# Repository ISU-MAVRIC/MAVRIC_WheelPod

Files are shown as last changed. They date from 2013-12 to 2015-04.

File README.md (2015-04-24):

MAVRIC_WheelPod
===============

Each MAVRIC Wheel Pod contains a motor controller driving the wheel along with a stepper to rotate the entire pod, steering the rover. This board controls these components in a compact, modular form factor. One will be located at each of the six wheel pods.

**Features:**
- STM32F4 Microcontroller
- PWM output to motor driver controlling wheel speed
- Current measurement on motor driver to measure wheel traction
- Stepper motor output to rotate the wheel pod, steering the rover
- Encoder analog in for steering position feedback, fed into a control loop
- RJ45 Jack for rx/tx control/status data as well as powering the wheel pod's 3V3 and 5V rails

##PCB Progress:
### Wheel Pod Board v1.0 ordered!
https://github.com/ISU-MAVRIC/MAVRIC_WheelPod/releases/tag/v1.0

Current Price: $12.60 for 3 boards, $4.20 each

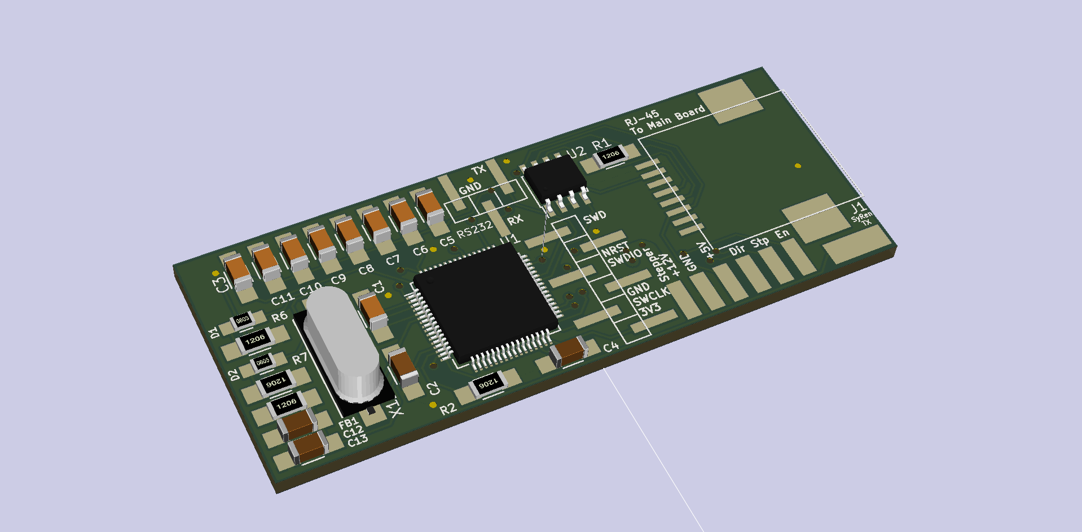
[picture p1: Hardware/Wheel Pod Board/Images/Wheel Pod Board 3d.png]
Board 3D


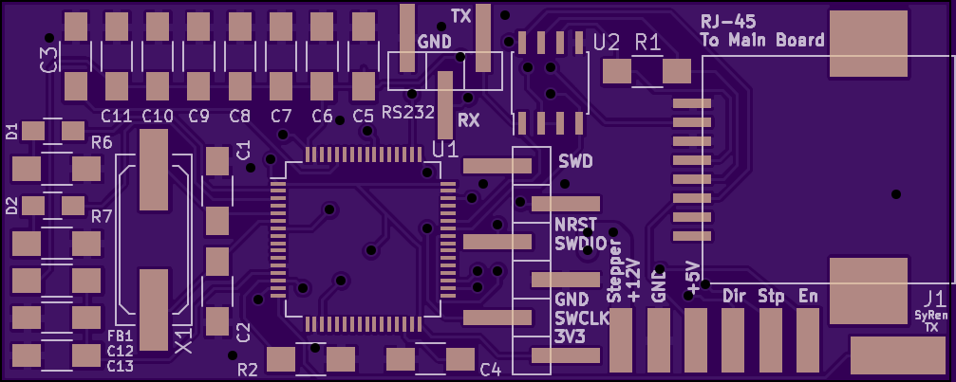
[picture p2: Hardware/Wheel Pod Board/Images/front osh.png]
'Wheel Pod Board Front
<br>
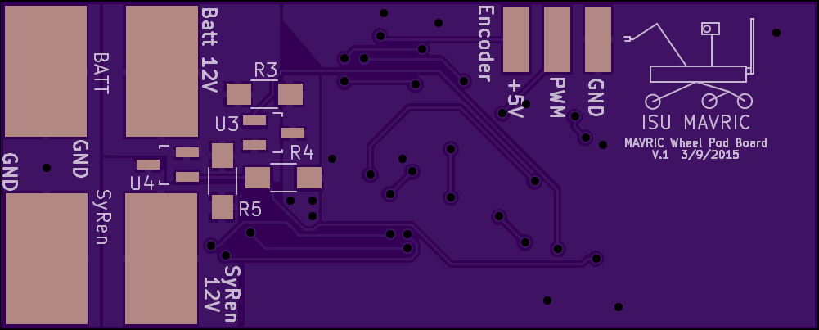
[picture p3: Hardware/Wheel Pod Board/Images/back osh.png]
Wheel Pod Board Back


### Grid Settings
- .5mm layout
- .5mm traces when possible, down to .25mm for detailed routing

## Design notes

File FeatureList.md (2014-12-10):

# Wheel Pod Feature List
## Hardware
- Full Duplex RS-485/RS-422 Converter 3.3V Supply
- _Intersil ISL83490IBZ_
- Half Duplex RS-485/RS-422 Transceiver 5V supply
- _STMicroelectronics ST485CDR_
- Hall Effect Current Transducer
- _Allegro MicroSystems ACS711ELCTR-25AB-T_
- Inductance to Digital Converter
- _Texas Instruments LDC1000_
- 3.3v Regulator
- _STMicroelectronics L78L33ACUTR_
- 5v Regulator (Required for analog voltage on LDC)
- _STMicroelectronics L78M05CDT-TR_
- Microcontroller
- _STMicroelectronics STM32F030K6T6_

## Features
- Cat5 jack for input from Chipkit (RS-485, 3.3V, GND)
- Stepper Motor current sense
- Wheel Motor current sense
- Serial connection to SyRen
- Connection to stepper controller (Enable, Direction, Step, 3.3V)
- Specification suggests 5V, any voltage is fine as long as current is between 5 - 20mA
- Inductance sensor for wheel rotation position

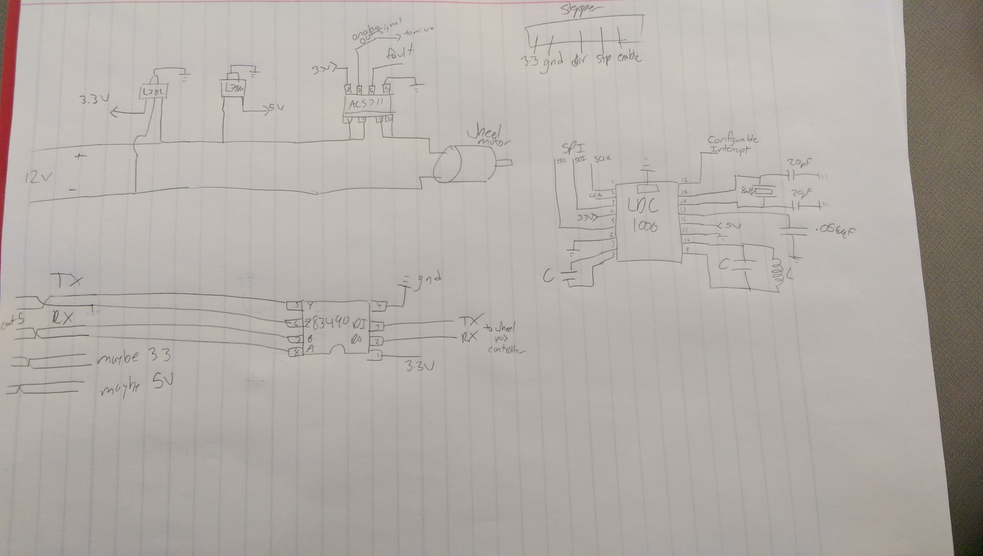
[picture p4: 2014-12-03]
Hardware/Diagrams/12-03-14 Schematic on Paper.jpg

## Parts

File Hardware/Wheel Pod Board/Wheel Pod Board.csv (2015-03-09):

Digi-Key Part Number | Customer Reference | Quantity 1
587-2254-1-ND | C4 C8 | 2
1276-2854-1-ND | C3 C5 C6 C7 C9 C10 C11 C12 | 8
240-2412-1-ND | FB1 | 1
399-8148-1-ND | C13 | 1
P100ECT-ND | R1 R6 R7 | 3
887-2439-1-ND | X1 | 1
1276-2809-1-ND | C2 C1 | 2
989-1025-1-ND | R3 | 1
P8.06KFCT-ND | R2 R4 | 2
696-1373-1-ND | R5 | 1
475-1415-1-ND | D1 | 1
475-1410-1-ND | D2 | 1

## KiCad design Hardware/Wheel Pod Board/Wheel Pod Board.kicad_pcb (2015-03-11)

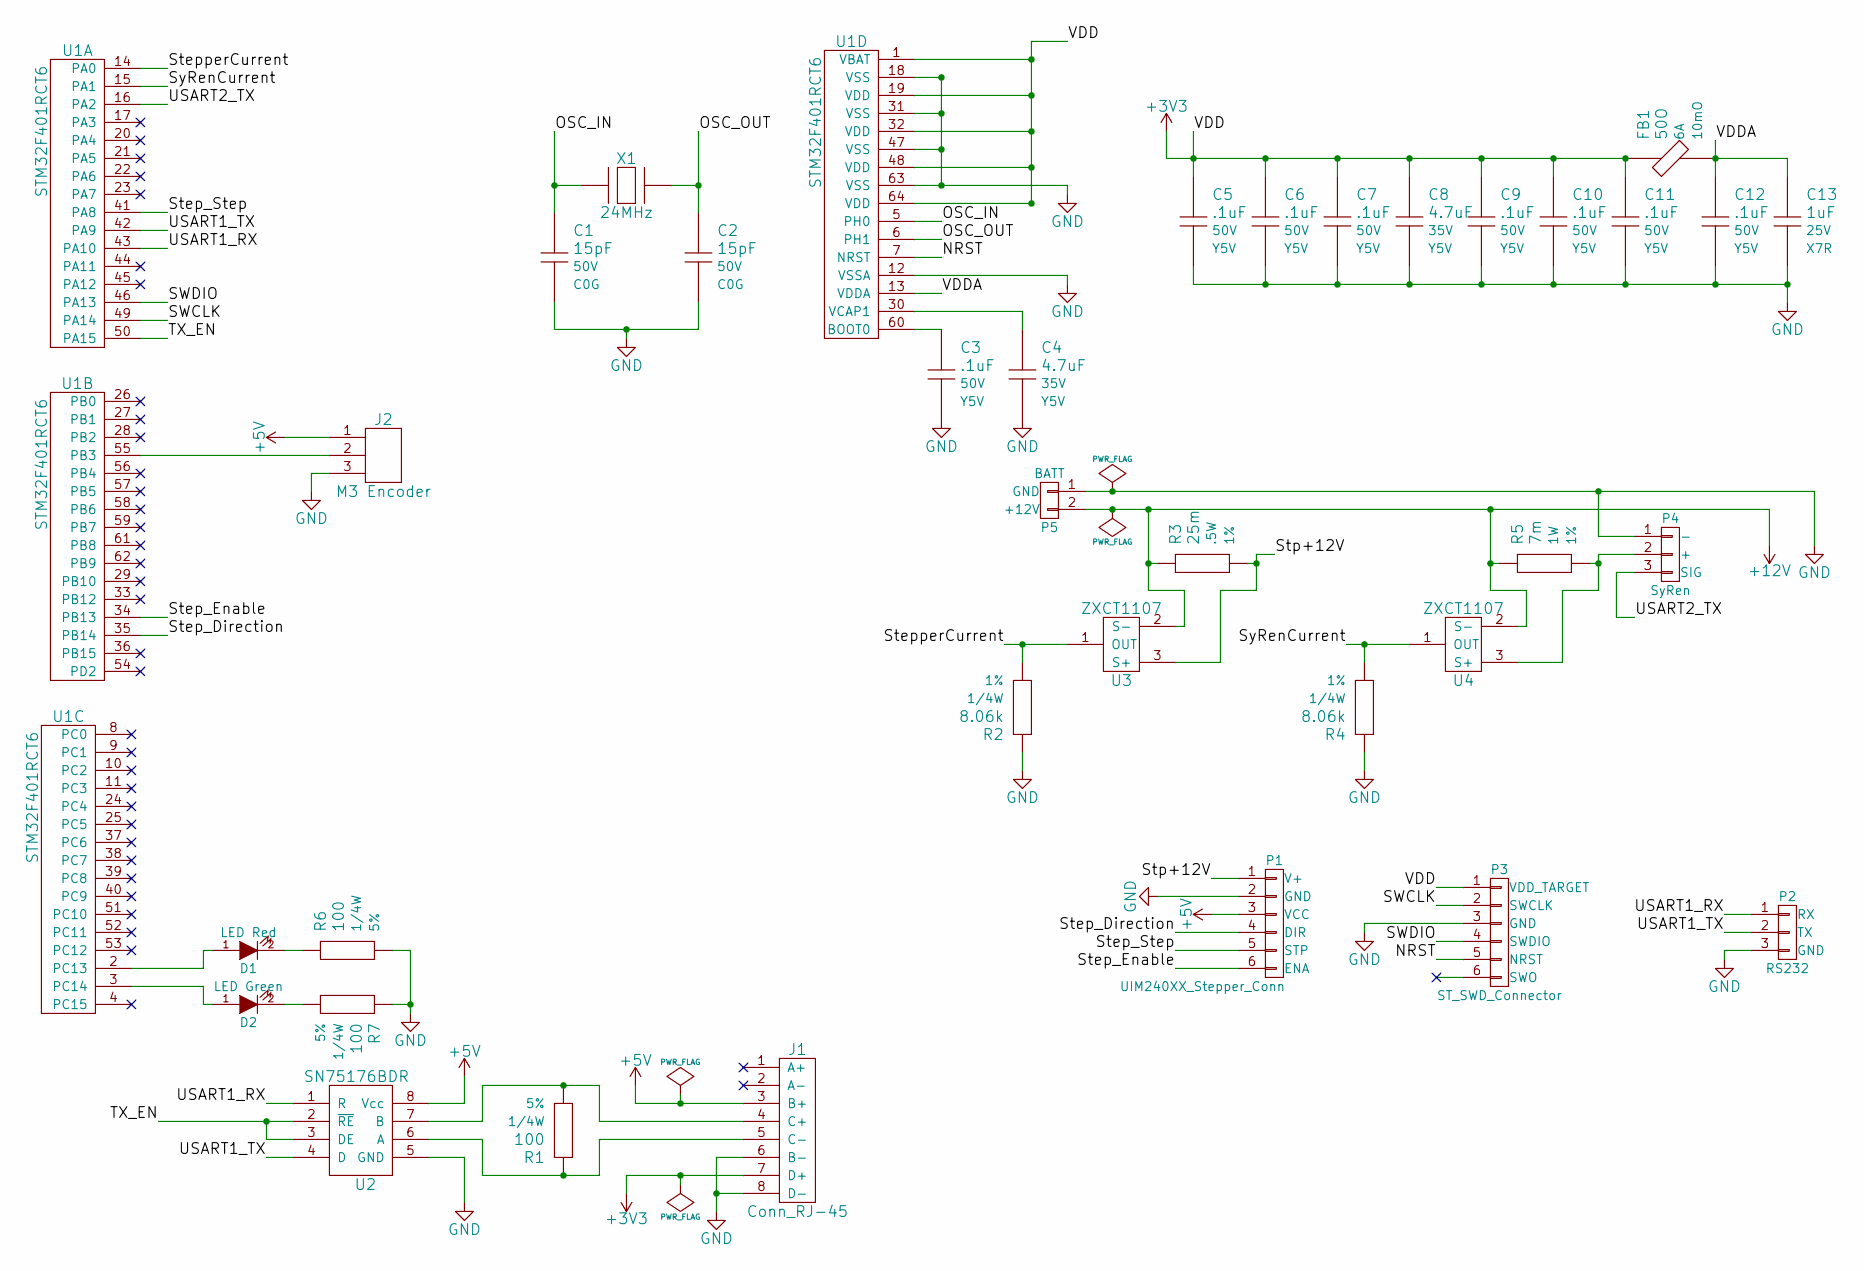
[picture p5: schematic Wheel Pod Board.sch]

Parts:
C1, C2: 15pF; C_1206_HandSoldering; Voltage 50V; Manufacturer Part # CL31C150JBCNNNC
C3, C5, C6, C7, C9, C10, C11, C12: .1uF; C_1206_HandSoldering; Voltage 50V; Manufacturer Part # CL31F104MBCNNNC
C4, C8: 4.7uF; C_1206_HandSoldering; Voltage 35V; Manufacturer Part # GMK316F475ZG-T
C13: 1uF; C_1206_HandSoldering; Voltage 25V; Manufacturer Part # C1206C105M3RACTU
D1: LED Red; R_0805_HandSoldering
D2: LED Green; R_0805_HandSoldering
FB1: 50O; R_1206_HandSoldering; Manufacturer Part # HI1206T500R-10
J1: Conn_RJ-45; Molex_RJ45_0437438101
J2: M3 Encoder; SolderWirePad_3x_0-8mmDrill
P1: UIM240XX_Stepper_Conn; 1x6_Breakaway_Header
P2: RS232; 1x3_Breakaway_Header
P3: ST_SWD_Connector; 1x6_Breakaway_Header
P4: SyRen; SolderWirePad_3x_0-8mmDrill
P5: BATT; SolderWirePad_2x_0-8mmDrill
R1, R6, R7: 100; R_1206_HandSoldering; Tolerance 5%; Manufacturer Part # ERJ-8GEYJ101V
R2, R4: 8.06k; R_1206_HandSoldering; Tolerance 1%; Manufacturer Part # ERJ-8ENF8061V
R3: 25m; R_1206_HandSoldering; Tolerance 1%; Manufacturer Part # LRC-LRF1206LF-01-R025F
R5: 7m; R_1206_HandSoldering; Tolerance 1%; Manufacturer Part # CSR1206-0R007F1
U1: STM32F401RCT6; LQFP-64_10x10mm_Pitch0.5mm
U2: SN75176BDR; SOIC-8_3.9x4.9mm_Pitch1.27mm
U3, U4: ZXCT1107; SOT23_Handsoldering
X1: 24MHz; Q_49U3HMS; Tolerance 30ppm; Manufacturer Part # 9C-24.000MAAE-T; Digi-Key Value

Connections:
+3V3: C5.1, C6.1, C7.1, C8.1, C9.1, C10.1, C11.1, FB1.1, J1.7 (D+), P3.1 (VDD_TARGET), U1.1 (VBAT), U1.19 (VDD), U1.32 (VDD), U1.48 (VDD), U1.64 (VDD)
+5V: J1.3 (B+), J2.1, P1.3 (VCC), U2.8 (Vcc)
+12V: P5.2 (+12V), R3.1, R5.1, U3.2 (S-), U4.2 (S-)
/NRST: P3.5 (NRST), U1.7 (NRST)
/OSC_IN: C1.1, U1.5 (PH0), X1.1
/OSC_OUT: C2.1, U1.6 (PH1), X1.2
/SWCLK: P3.2 (SWCLK), U1.49 (PA14)
/SWDIO: P3.4 (SWDIO), U1.46 (PA13)
/Step_Direction: P1.4 (DIR), U1.35 (PB14)
/Step_Enable: P1.6 (ENA), U1.34 (PB13)
/Step_Step: P1.5 (STP), U1.41 (PA8)
/StepperCurrent: R2.2, U1.14 (PA0), U3.1 (OUT)
/Stp+12V: P1.1 (V+), R3.2, U3.3 (S+)
/SyRenCurrent: R4.2, U1.15 (PA1), U4.1 (OUT)
/TX_EN: U1.50 (PA15), U2.2 (~RE), U2.3 (DE)
/USART1_RX: P2.1 (RX), U1.43 (PA10), U2.1 (R)
/USART1_TX: P2.2 (TX), U1.42 (PA9), U2.4 (D)
/USART2_TX: P4.3 (SIG), U1.16 (PA2)
/VDDA: C12.1, C13.1, FB1.2, U1.13 (VDDA)
GND: C1.2, C2.2, C3.2, C4.2, C5.2, C6.2, C7.2, C8.2, C9.2, C10.2, C11.2, C12.2, C13.2, J1.6 (B-), J1.8 (D-), J2.3, P1.2 (GND), P2.3 (GND), P3.3 (GND), P4.1 (-), P5.1 (GND), R2.1, R4.1, R6.2, R7.1, U1.12 (VSSA), U1.18 (VSS), U1.31 (VSS), U1.47 (VSS), U1.63 (VSS), U2.5 (GND)
unnamed: C3.1, U1.60 (BOOT0)
unnamed: C4.1, U1.30 (VCAP1)
unnamed: D1.1 (A), U1.2 (PC13)
unnamed: D1.2 (K), R6.1
unnamed: D2.1 (A), U1.3 (PC14)
unnamed: D2.2 (K), R7.2
unnamed: J1.4 (C+), R1.2, U2.7 (B)
unnamed: J1.5 (C-), R1.1, U2.6 (A)
unnamed: J2.2, U1.55 (PB3)
unnamed: P4.2 (+), R5.2, U4.3 (S+)

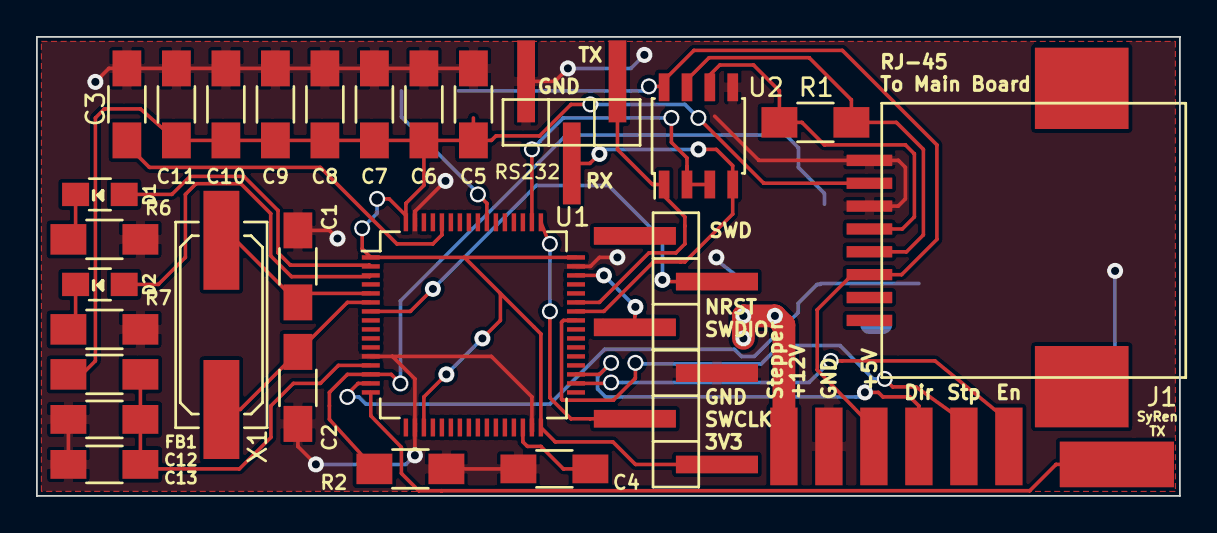
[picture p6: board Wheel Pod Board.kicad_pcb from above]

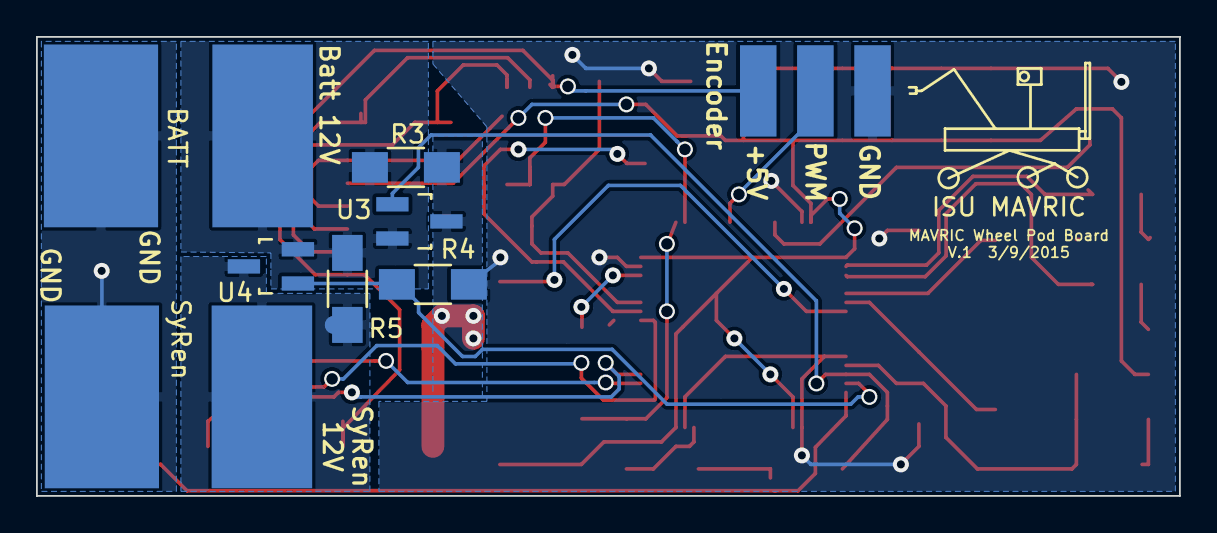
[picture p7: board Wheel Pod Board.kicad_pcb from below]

Board: 2 copper layers, 63.5 x 25.5 mm, 36 parts (9 on the bottom side), 30 nets.

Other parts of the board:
ISU MAVRIC: VAL**; MAVRIC_LOGO

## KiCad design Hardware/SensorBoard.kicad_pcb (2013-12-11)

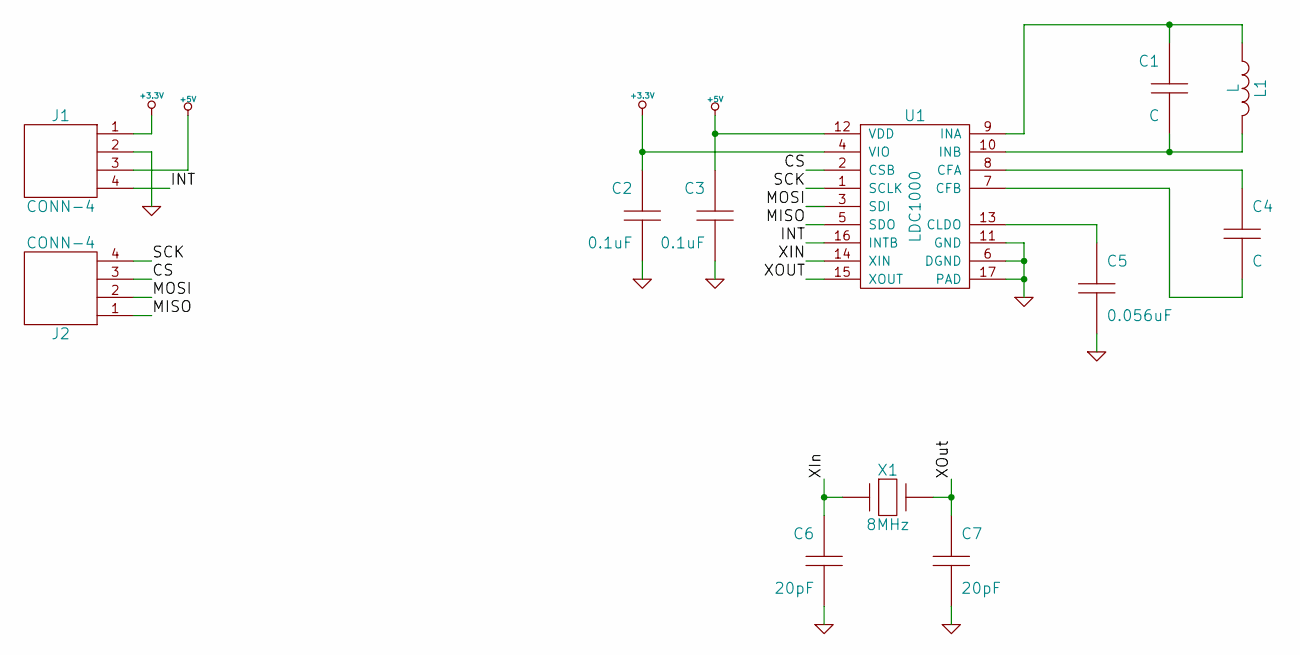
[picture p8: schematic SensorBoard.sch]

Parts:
C1, C4: C; Voltage V
C2, C3: 0.1uF; CAPC1608-N; Voltage 16V; MFR Part No CL10B104KO8NNNC
C5: 0.056uF; CAPC1608-N; Voltage 50V; MFR Part No CL10B563KB8SFNC
C6, C7: 20pF; CAPC1608-N; Voltage 100V; MFR Part No GRM1885C2A200JA01D
J1, J2: CONN-4
L1: L
U1: LDC1000
X1: 8MHz; MFR Part No CX5032GB08000H0HEQZ1

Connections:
+3.3V: C2.1, J1.1, U1.4 (VIO)
+5V: C3.1, J1.3, U1.12 (VDD)
/CS: J2.3, U1.2 (CSB)
/INT: J1.4, U1.16 (INTB)
/MISO: J2.1, U1.5 (SDO)
/MOSI: J2.2, U1.3 (SDI)
/SCK: J2.4, U1.1 (SCLK)
/XIN: C6.1, U1.14 (XIN), X1.1
/XOUT: C7.1, U1.15 (XOUT), X1.2
GND: C2.2, C3.2, C5.2, C6.2, C7.2, J1.2, U1.6 (DGND), U1.11 (GND), U1.17 (PAD)
unnamed: C1.2, L1.1, U1.10 (INB)
unnamed: C1.1, L1.2, U1.9 (INA)
unnamed: C4.2, U1.7 (CFB)
unnamed: C4.1, U1.8 (CFA)
unnamed: C5.1, U1.13 (CLDO)

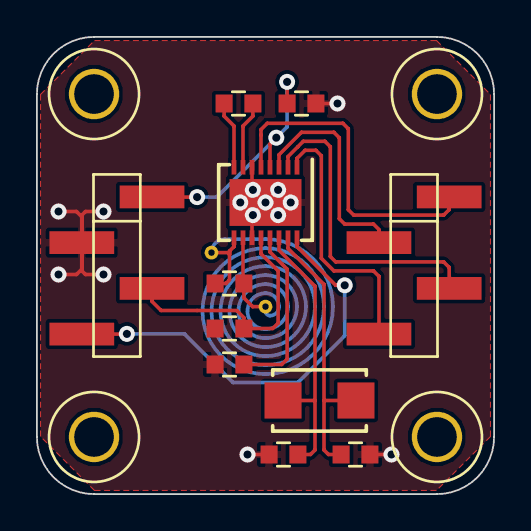
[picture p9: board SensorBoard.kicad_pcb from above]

Board: 2 copper layers, 25.4 x 25.4 mm, 16 parts (1 on the bottom side), 15 nets.

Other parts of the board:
MECH-HOLE220, MECH-HOLE220#2, MECH-HOLE220#3, MECH-HOLE220#4: VAL**; MECH-HOLE220

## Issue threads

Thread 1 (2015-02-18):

Find absolute feedback solution for rotation

markrusciano, 2015-02-18:
Maybe some kind of continuous absolute encoder like this hooked up to a belt/gear system with the limited clearance beneath/within the gearbox.
http://www.digikey.com/product-detail/en/EAW0J-C24-AE0128L/EAW0J-C24-AE0128L-ND/3780126

Random Links
- http://www.usdigital.com/products/encoders/absolute/rotary/shaft/ma3
- https://www.youtube.com/watch?v=6r2ZThBgSOc

markrusciano, 2015-02-18:
@ethanharstad what do you think of maybe having a small belt with a 1:1 ratio between the shaft of the gearbox and a potentiometer/encoder? Seems like it could be simple and space efficient provided we'd be able to protect the belt from dust in some way

ethanharstad, 2015-02-18:
The problem with belts/gears is that to have a 1:1 ratio we need to have the encoder wheel the same size as the the part of the output shaft that it attaches to. Anything else, by geometry would not have a 1:1 ratio. It is possible we could go for a 2:1 ratio with that digital encoder, that would give us absolute positioning over a 180 degree range but we could dead reckon outside of that range, we would just have to have the wheel pointing +/- 90 degrees from 'forward' when we turn it on. Similarly we could probably get away with up to maybe 6:1 ratio and have to be aligned +/- 30 degrees.

markrusciano, 2015-02-18:
what about a 360 degree continuous encoder? we could do the 6:1 there and just handle the loop around from 359 to 0

markrusciano, 2015-02-18:
@JDD314 some ideas for feedback

markrusciano, 2015-02-19:
Perhaps this: http://www.usdigital.com/products/encoders/absolute/rotary/kit/MAE3
gotta go to class, will add more later

markrusciano, 2015-03-05:
Going with this one for now: http://www.usdigital.com/products/encoders/absolute/rotary/shaft/ma3

markrusciano, 2015-03-05:
Also something interesting:
http://www.digikey.com/en/product-highlight/b/bourns/rotary-position-sensors

Closed 2015-03-05.

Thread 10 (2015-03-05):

Determine mounting hole spacing/size

markrusciano, 2015-03-05:
@JDD314 we'll need to coordinate on how we want to attach this

tkminer, 2015-03-05:
mark why do i only get these from you

On Wed, Mar 4, 2015 at 11:05 PM, Mark Rusciano <notifications@github.com>
wrote:

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

markrusciano, 2015-03-05:
I've just been making a lot of issues. I believe you can unsubscribe from this repository or unwatch it if they are bothering you.

tkminer, 2015-03-05:
oh i will i will you'll see you'll all see

On Wed, Mar 4, 2015 at 11:14 PM, Mark Rusciano <notifications@github.com>
wrote:

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

markrusciano, 2015-03-08:
Going to heat shrink the board and attach it with zip ties

Closed 2015-03-08.

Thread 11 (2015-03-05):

Create skeleton code similar to main board

markrusciano, 2015-03-05:
- [ ] PWM for stepper direction
- [ ] General out for Stepper_Step, Stepper_Enable, 3V3_Enable, 5V_Enable, 485_TX
- [ ] Analog in for Stepper_Current, SyRen_Current
- [ ] PWM out for RGB LED (one for red, blue, green)

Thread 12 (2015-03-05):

Fix footprints

markrusciano, 2015-03-05:
Some component footprints are broken from the copy-paste from the main board

Closed 2015-03-06.

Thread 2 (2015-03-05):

Connectors to add

markrusciano, 2015-03-05:
- [x] Battery connector (maybe think of something better than Arm Board)
- [x] 232 jack between micro and 485 transceiver

Closed 2015-03-05.

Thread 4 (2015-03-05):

Rough PCB component positioning

markrusciano, 2015-03-05:
Board outline is 1 inch by not too long

Closed 2015-03-06.

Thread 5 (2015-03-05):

Add cat5 jack for ethernet

markrusciano, 2015-03-05:
- [x] Find horizontal (plugs in parallel to board) rj45 connector on Digi-Key (comment with part nums)
- [x] Create schematic part in MAVRIC_Lib (add fields for vendor and vendor part num)
   - didn't need to, aerodyne lab's kicadlib has one in connectors
- [x] Wire in schematic (Pin 5 - 485A | Pin 4 - 485B | Pin 7 - GND | Pin 8 - GND )
- [x] Create footprint for jack
- [x] Add to PCB if complete

markrusciano, 2015-03-05:
http://www.digikey.com/product-detail/en/0437438101/WM6469CT-ND/2816114

Closed 2015-03-06.

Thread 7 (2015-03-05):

Add RGB LED

markrusciano, 2015-03-05:
- [x] Find RGB LED on Digi-Key (post part in comments)
- [ ] Create schematic part in MAVRIClib
- [ ] Connect PWM pins to any PWM pins on the STM32
- [ ] Update the pins you used on the STM32 in the STM32Cube project (set as timers then pwm)
- [ ] Create footprint if one doesn't already exist

markrusciano, 2015-03-05:
Maybe this http://www.digikey.com/product-detail/en/CLVBA-FKA-CAEDH8BBB7A363/CLVBA-FKA-CAEDH8BBB7A363CT-ND/2650500

markrusciano, 2015-03-08:
Added a red and a green LED

Closed 2015-03-08.

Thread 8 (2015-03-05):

Route PCB

markrusciano, 2015-03-05:
Try to do the horizontal/vertical trace layer separation

markrusciano, 2015-03-06:
First route is done but there is a lot to improve

Closed 2015-03-07.

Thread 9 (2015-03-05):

Find better battery connector solution

markrusciano, 2015-03-05:

markrusciano, 2015-03-06:
Thinking a pigtail soldered to some rectangular pads with some easy to plug/unplug connector

Closed 2015-03-06.

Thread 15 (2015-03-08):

Make sure 485 transceiver output won't fry the stm32

markrusciano, 2015-03-08:

markrusciano, 2015-03-09:
yeah turns out almost every pin is 5V tolerant so we are golden

Closed 2015-03-09.

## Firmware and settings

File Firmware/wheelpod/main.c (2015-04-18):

#include "stm32f4xx.h"
#include "stm32f4xx_gpio.h"
#include "stm32f4xx_rcc.h"
#include "stm32f4xx_tim.h"
#include "misc.h"

void TIM_Config(void)
{
	GPIO_InitTypeDef GPIO_InitStructure;

	RCC_APB1PeriphClockCmd(RCC_APB1Periph_TIM5, ENABLE);
	RCC_AHB1PeriphClockCmd(RCC_AHB1Periph_GPIOA, ENABLE);

	GPIO_InitStructure.GPIO_Pin = GPIO_Pin_2;
	GPIO_InitStructure.GPIO_Mode = GPIO_Mode_AF;
	GPIO_InitStructure.GPIO_Speed = GPIO_Speed_100MHz;
	GPIO_InitStructure.GPIO_OType = GPIO_OType_PP;
	GPIO_InitStructure.GPIO_PuPd = GPIO_PuPd_UP;
	GPIO_Init(GPIOA, &GPIO_InitStructure);

	GPIO_PinAFConfig(GPIOA, GPIO_PinSource2, GPIO_AF_TIM5);

}

int main(void) {

	TIM_Config();

	RCC_HSEConfig(RCC_HSE_ON);

	GPIO_InitTypeDef GPIO_InitStructure;
	TIM_TimeBaseInitTypeDef TIM_TimeBaseStructure;
	TIM_OCInitTypeDef TIM_OCInitStructure;


	RCC_AHB1PeriphClockCmd(RCC_AHB1Periph_GPIOC, ENABLE);

	GPIO_InitStructure.GPIO_Pin = GPIO_Pin_14;
	GPIO_InitStructure.GPIO_Speed = GPIO_Speed_100MHz;
	GPIO_InitStructure.GPIO_Mode = GPIO_Mode_OUT;
	GPIO_InitStructure.GPIO_OType = GPIO_OType_PP;
	GPIO_InitStructure.GPIO_PuPd = GPIO_PuPd_UP;
	GPIO_Init(GPIOC, &GPIO_InitStructure);

	RCC_MCO1Config(RCC_MCO1Source_HSE, RCC_MCO1Div_1);

	//TIM5's clock is set to 2x the APB1 Clock
	//Since the APB1 clock is 42MHz, our TIM5 clock is 84MHz
	//We want to prescale this to something a little bit more
	//user friendly.

	TIM_TimeBaseStructure.TIM_Period = 20000;
	TIM_TimeBaseStructure.TIM_Prescaler = 15;
	TIM_TimeBaseStructure.TIM_ClockDivision = 0;
	TIM_TimeBaseStructure.TIM_CounterMode = TIM_CounterMode_Up;
	TIM_TimeBaseInit(TIM5, &TIM_TimeBaseStructure);

	TIM_OCInitStructure.TIM_OCMode = TIM_OCMode_PWM1;
	TIM_OCInitStructure.TIM_OutputState = TIM_OutputState_Enable;
	TIM_OCInitStructure.TIM_OCPolarity = TIM_OCPolarity_High;
	TIM_OCInitStructure.TIM_Pulse = 1500;

	TIM_OC3Init(TIM5, &TIM_OCInitStructure);
	TIM_OC3PreloadConfig(TIM5, TIM_OCPreload_Enable);

	TIM_ARRPreloadConfig(TIM5, ENABLE);
	TIM_Cmd(TIM5, ENABLE);



	while (1) {
		GPIO_ToggleBits(GPIOC, GPIO_Pin_14);

		int nCount = 400000;

		while (nCount != 0) {
			nCount--;
		}
	}
}

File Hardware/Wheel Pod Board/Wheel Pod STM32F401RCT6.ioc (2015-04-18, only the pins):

Mcu.UserName=STM32F401RCTx
PA0-WKUP.GPIO_Label=Stepper Current In
PA0-WKUP.Signal=ADCx_IN0
PA1.GPIO_Label=Victor Current In
PA1.Signal=ADCx_IN1
PA10.Signal=USART1_RX
PA13.Signal=SYS_JTMS-SWDIO
PA14.Signal=SYS_JTCK-SWCLK
PA15.GPIO_Label=485 TX Enable
PA15.Signal=GPIO_Output
PA2.GPIO_Label=Victor PWM Out
PA2.Signal=S_TIM5_CH3
PA8.GPIO_Label=Stepper Step
PA8.Signal=S_TIM1_CH1
PA9.Signal=USART1_TX
PB13.GPIO_Label=Stepper Enable
PB13.Signal=GPIO_Output
PB14.GPIO_Label=Stepper Direction
PB14.Signal=GPIO_Output
PB3.GPIO_Label=Steering Pos Fdbk PWM In
PB3.Signal=S_TIM2_CH2
PC13-ANTI_TAMP.GPIO_Label=Red LED
PC13-ANTI_TAMP.Signal=GPIO_Output
PC14-OSC32_IN.GPIO_Label=Green LED
PC14-OSC32_IN.Signal=GPIO_Output

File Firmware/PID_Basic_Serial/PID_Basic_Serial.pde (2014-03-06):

#include <SyRenSimplified.h>

/********************************************************
 * PID Basic Example
 * Reading analog Input 0 to control analog PWM rawOutput 3
 ********************************************************/

#include <PID_v1.h>

//Define Variables we'll be connecting to
double setPoint, input, rawOutput;
double rawInput, output;

//Specify the links and initial tuning parameters
//Input range 00008-1023
PID myPID(&input, &rawOutput, &setPoint,1.2,0,0, DIRECT);

//String dataString;

SyRenSimplified SR(Serial2);

  char received[3];
  int i = 0;

void setup()
{
  Serial.begin(9600);
  Serial2.begin(9600);
  //initialize the variables we're linked to
  rawInput = analogRead(0);
  setPoint = 300;

  //turn the PID on
  myPID.SetOutputLimits(-127,127);
  myPID.SetMode(AUTOMATIC);
}

void loop()
{
  rawInput = analogRead(0);
  input = map(rawInput,102,1023,0,1023);
  myPID.Compute();
  int intrawOutput = (int) rawOutput;
  SR.motor(intrawOutput);
  Serial.print("Input: ");
  Serial.print(input);
  Serial.print("\t Output: ");
  Serial.println(intrawOutput);
  

  if(Serial.available() > 0)
  {
    char ch = Serial.read();
    if(i <= 2 && isDigit(ch))
    {
      received[i++] = ch;
    }
    else
    {
      received[i] = ch;
      setPoint = atoi(received);
      Serial.println(setPoint);
      i = 0;
    }
  }
}

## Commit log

2013-11-16 Create kicad project
    [WheelPod.sch]
2013-11-16 Simple schematic/board for sizing purposes
    [WheelPod.kicad_pcb, WheelPod.sch]
2013-11-22 Split into separate boards
    [SensorBoard.sch, WheelPod.kicad_pcb, WheelPod.sch]
2013-12-11 Finish Sensor Board
    [SensorBoard.kicad_pcb, SensorBoard.sch, WheelPod.kicad_pcb]
2014-02-06 Added PID Test firmware
2014-02-11 Added PID arm firmware
    Untested code. Currently will convert cartesian commands to polar
    positions and sets PIDs to update to those positions.
2014-02-12 PID Output was properly ranged
2014-02-19 Modified for serial motor control
2014-02-22 Tuned PID
2014-03-06 Tuned PID Coefficients
2014-03-13 Motor control commands are now packetized serial
2014-12-02 WheelPod Power Board Beginnings
    The fumblings of a KiCad rookie made available to the public
2014-12-03 Very Rough Schematic Created
    Just a photo of a pencil drawing, will be drawn digitally soon
2014-12-10 Created MAVRIC part library and new schematic
    New schematic will likely transform into something different in the
    future
    [Microcontroller.sch]
2014-12-11 Added LDC to schematic
    [Microcontroller.sch]
2015-02-20 Start new schematic and PCB layout
    [Microcontroller.sch, SensorBoard.kicad_pcb, SensorBoard.sch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]
2015-03-05 Import common blocks from Arm Board
    [Power.sch, Wheel Pod Board.sch]
2015-03-05 Connect some power, create STMCube project
    [Wheel Pod Board.sch]
2015-03-05 Connect current sense, more connectors
    Resistor values not correct #6
    Resolve #2
    [Power.sch, Wheel Pod Board.sch]
2015-03-05 Calculate current sense, parts on PCB
    Resolves #6
    [Power.sch, Wheel Pod Board.sch]
2015-03-05 More parts on PCB
    [Power.sch, Wheel Pod Board.kicad_pcb, Wheel Pod Board.sch]
2015-03-06 Connect 485 to RJ45 jack on schematic
    #5
    [Wheel Pod Board.sch]
2015-03-06 Fix footprints, add RJ45 jack to pcb
    Resolve #12, Resolve #5
    [Wheel Pod Board.kicad_pcb, Wheel Pod Board.sch]
2015-03-06 Reroute 3V3 and 5V through cat5, remove regs
    [Wheel Pod Board.kicad_pcb, Wheel Pod Board.sch]
2015-03-06 Make STM32 connections, fix DRC errors
    [Wheel Pod Board.sch]
2015-03-06 Update cube, make connections to microcontroller
    [Wheel Pod Board.kicad_pcb, Wheel Pod Board.sch]
2015-03-06 Position components on PCB
    Closes #4
    [Wheel Pod Board.kicad_pcb, Wheel Pod Board.sch]
2015-03-06 Begin routing PCB
    Starting #8
    [Wheel Pod Board.kicad_pcb]
2015-03-06 Route all components, generate export + images
    Progressing #8, Close #9 for now
    [Wheel Pod Board-B_Cu.gbl, Wheel Pod Board-B_Mask.gbs, Wheel Pod Board-B_SilkS.gbo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]
2015-03-06 Add ADC channels to cube, kicad something
    [Wheel Pod Board.sch]
2015-03-07 Progress on new pcb route
    [Wheel Pod Board.kicad_pcb, Wheel Pod Board.sch]
2015-03-07 Finish PCB reroute one
    Resolve #8, resolve #13
    [Wheel Pod Board-B_Cu.gbl, Wheel Pod Board-B_Mask.gbs, Wheel Pod Board-B_SilkS.gbo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]
2015-03-07 Attach 485 TX enable to micro
    [Wheel Pod Board-B_Cu.gbl, Wheel Pod Board-B_Mask.gbs, Wheel Pod Board-B_SilkS.gbo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]
2015-03-07 Fixed SyRen TX pad layers
    [Wheel Pod Board.kicad_pcb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]
2015-03-07 Update images to pcb route v2
2015-03-07 Update board price on readme
2015-03-08 Add red and green LEDs to board
    [Wheel Pod Board.kicad_pcb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]
2015-03-08 Change out SWD footprint to new breakaway header
    [Wheel Pod Board-B_Cu.gbl, Wheel Pod Board-B_Mask.gbs, Wheel Pod Board-B_SilkS.gbo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]
2015-03-08 Change 232 header to new breakaway footprint
    what a mess
    [Wheel Pod Board-B_Cu.gbl, Wheel Pod Board-B_Mask.gbs, Wheel Pod Board-B_SilkS.gbo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]
2015-03-08 Change header footprints to new ones in schematic
    Forgot to save this until now, did this before I made the PCB changes
    [Wheel Pod Board.sch]
2015-03-09 Add pads for connecting encoder
    Schematic, PCB, and in cube
    Resolves #16
    [Wheel Pod Board.kicad_pcb, Wheel Pod Board.sch]
2015-03-09 Add resistor for green LED, clean up references
    [Wheel Pod Board.kicad_pcb, Wheel Pod Board.sch]
2015-03-09 Create BOM, send exports to fab
    [Wheel Pod Board.csv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]
2015-03-09 Update board images for v1.0 fab
2015-03-09 Update readme for v1.0 board order info
2015-03-11 Fix LED polarity
    [Wheel Pod Board.kicad_pcb, Wheel Pod Board.sch]
2015-04-02 Working LED blink test firmware
2015-04-11 Add cube labels, SyRen TX changed to Victor PWM out
2015-04-11 Add some really excellent not working PWM code
    hire me
    [main.c, startup_stm32f4xx.c]
2015-04-18 Add wheelpod project with working timers
2015-04-18 Update timer values to match servo pwm period
2015-04-18 Fix pwm out for servo
    Forgot to save before last commit.
    [main.c]
